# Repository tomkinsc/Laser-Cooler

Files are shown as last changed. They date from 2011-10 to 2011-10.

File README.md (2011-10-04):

(Scroll down for images)

This project includes CAD designs for a custom water cooling box with radiator, pump, and fans. It is intended to cool a 40W hobby laser cutter.

This was created to replace a bucket used for cooling. The open water grew algae, and when the bucket system heated up, only passive radiation could cool it.

This design improves cooling, and is constructed using laser-cut plywood, fittings from the hardware store, and commodity PC water cooling parts. It sports variable fan speed, an on/off switch, and a water reservoir. The setup is powered by a computer power supply.

The tolerances are not as tight as they could be, but it works fine.  The panels are held together with M3x16 socket cap screws. The screws are used similar to how they are in the MakerBot design. The side panels are held by friction, but tape can be added to secure them. A future revision might include screws along those edges as well. The tubing is 3/8 ID black vinyl. It's pretty tight inside the box, so correct tubing length is important.

The box is made from 5.5mm Tri-ply from the local big box home improvement store. The enclosure was designed in DraftSight, and cut using my 40W hobby laser. The enclosure is designed to accommodate the following parts (Newegg part numbers):

* 2x Enzotech HF-G1/4-38 Water Cooling Accessory (#N82E16835708034)
* 1x NZXT Sentry-2 5.25" Touch Screen fan controller (#N82E16811992005)
* 1x Swiftech MCP355 12 VDC Pump (#N82E16835108097)
* 1x Rosewill SL-300TFX 300W TFX12V Power Supply - OEM (#N82E16817182207)
* 2x Scythe SY1225SL12SH 120mm "Slipstream" Case Fan (#N82E16835185060)
* 1x Swiftech MCR220-QP Liquid Cooler Radiator (#N82E16835108086)
* 1x Regular GE wall switch
* 1x Reservoir assembly fashioned from PVC pipe and brass fittings.

The main power switch closes a circuit between lines 14 and 15 on the ATX power supply connector. This turns the supply on. The coolant loop travels as follows: reservoir-->pump->laser tube->radiator->reservoir. It is important to prime the pump so that it does not self destruct. A drain valve on the pump out line works well for this, if the valve is located below the reservoir.

The files are released under a Creative Commons Attribution-NonCommercial-ShareAlike 3.0 Unported License.

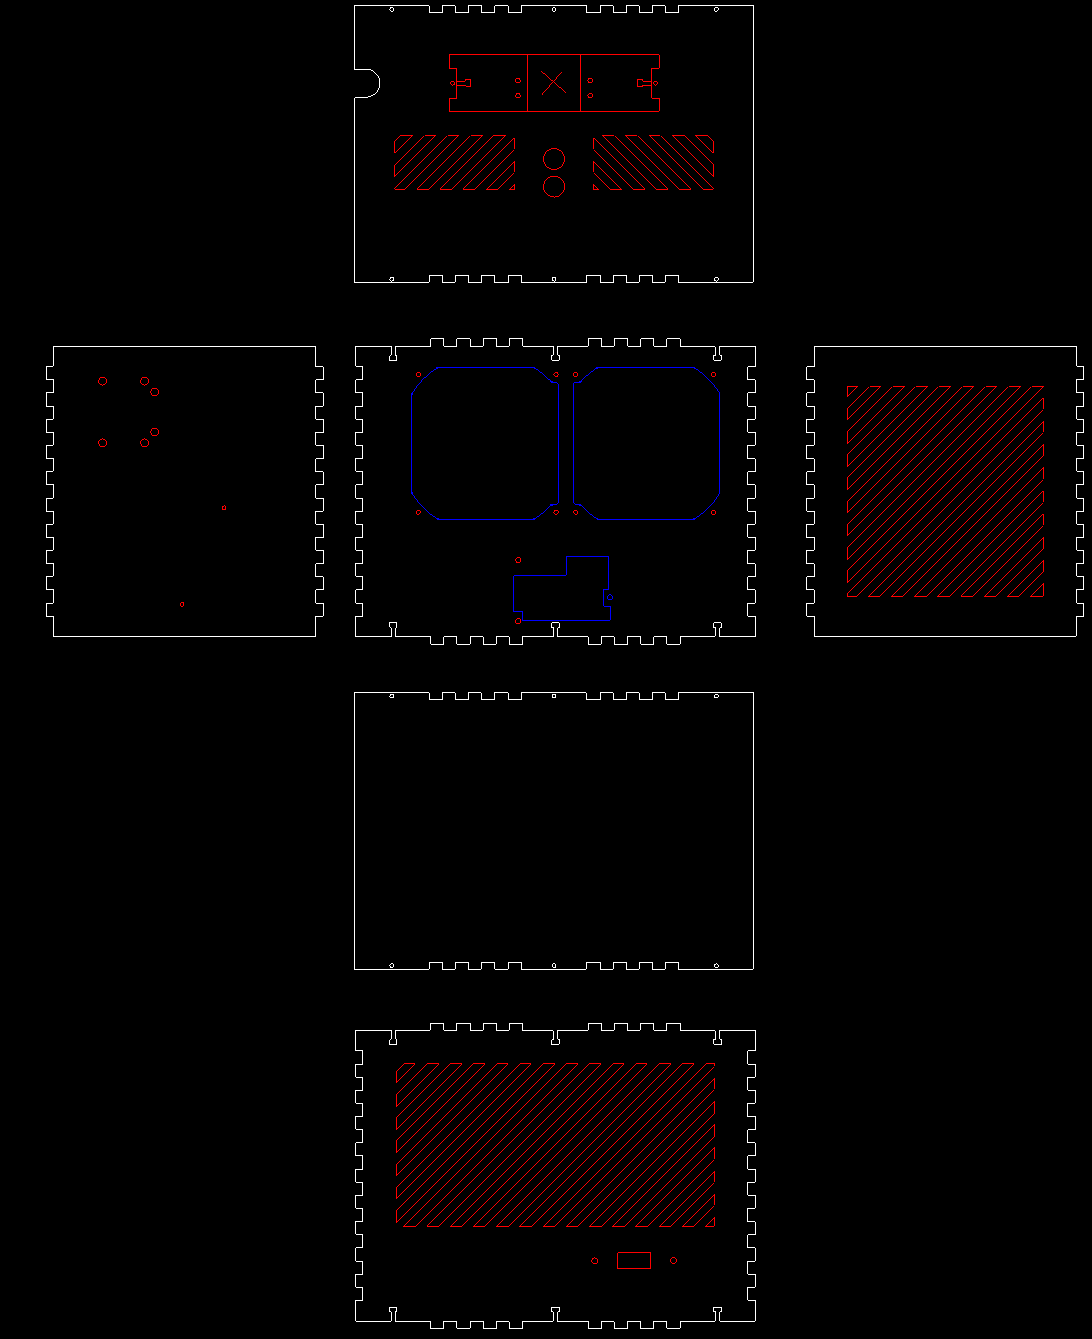
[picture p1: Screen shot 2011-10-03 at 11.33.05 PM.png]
 
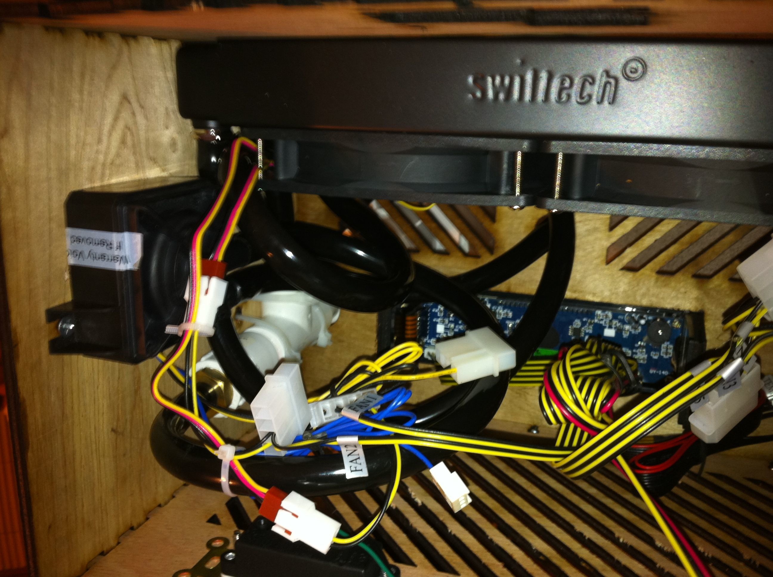
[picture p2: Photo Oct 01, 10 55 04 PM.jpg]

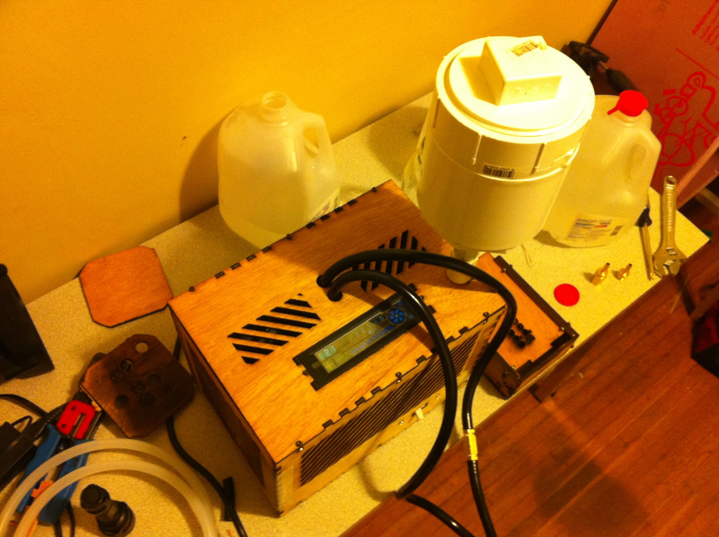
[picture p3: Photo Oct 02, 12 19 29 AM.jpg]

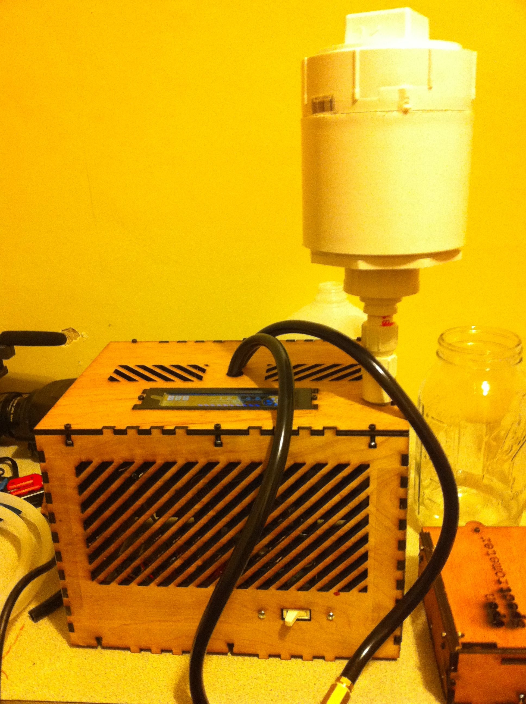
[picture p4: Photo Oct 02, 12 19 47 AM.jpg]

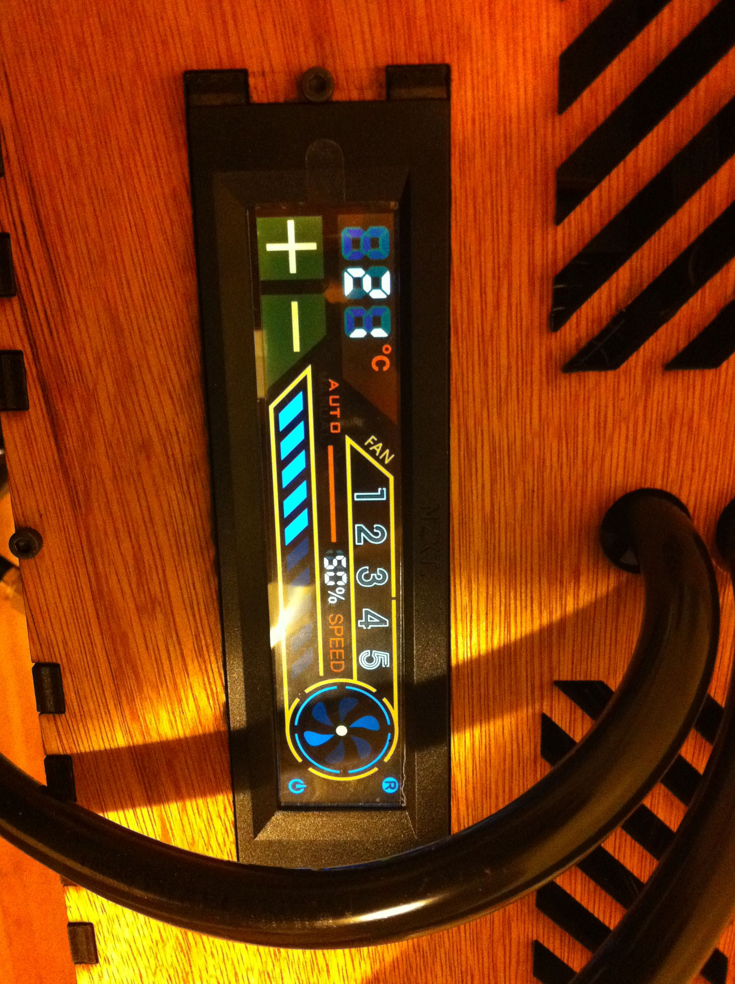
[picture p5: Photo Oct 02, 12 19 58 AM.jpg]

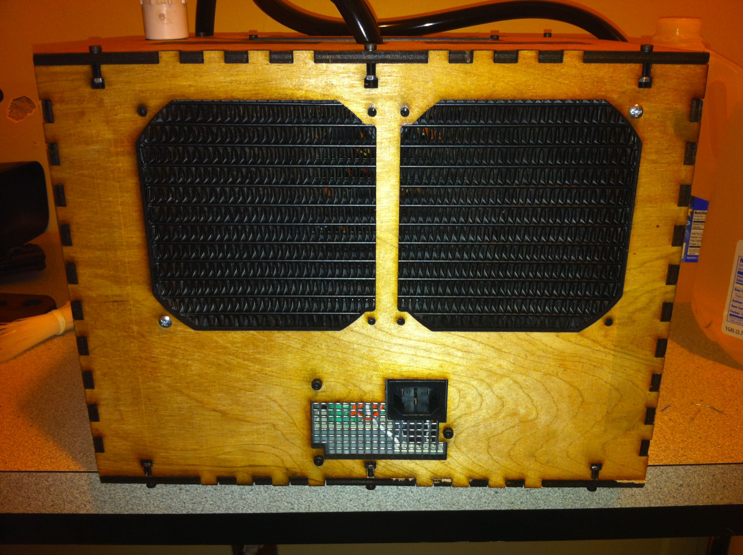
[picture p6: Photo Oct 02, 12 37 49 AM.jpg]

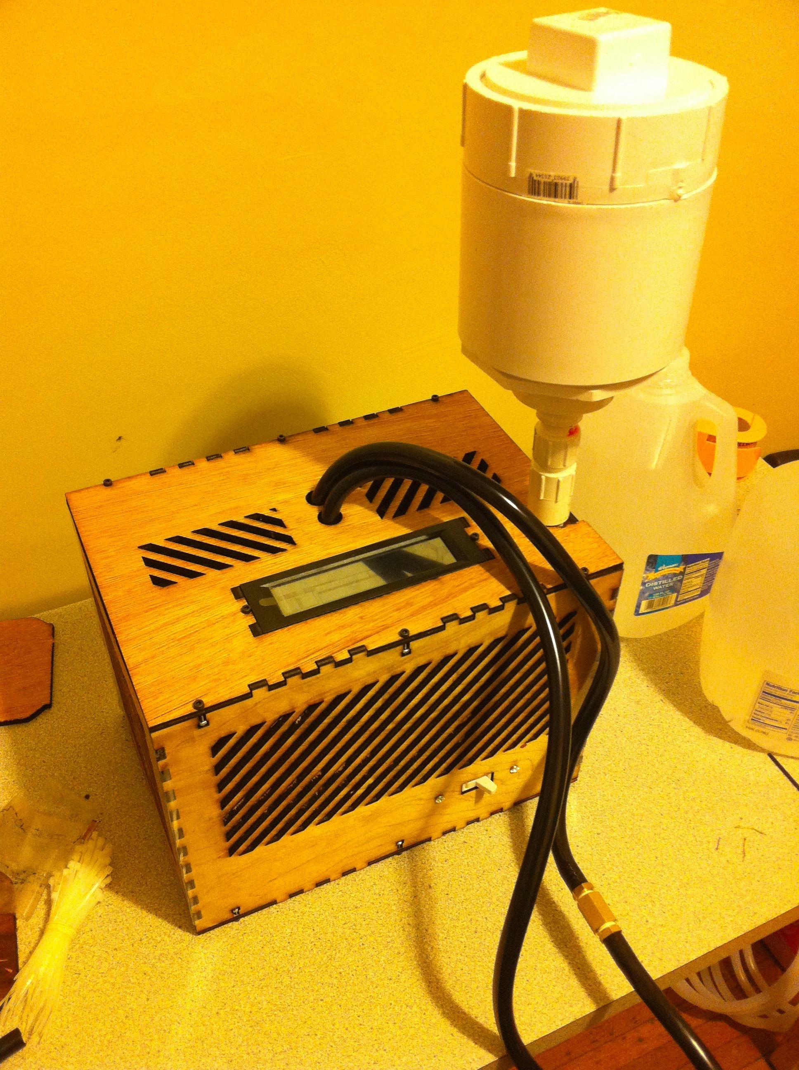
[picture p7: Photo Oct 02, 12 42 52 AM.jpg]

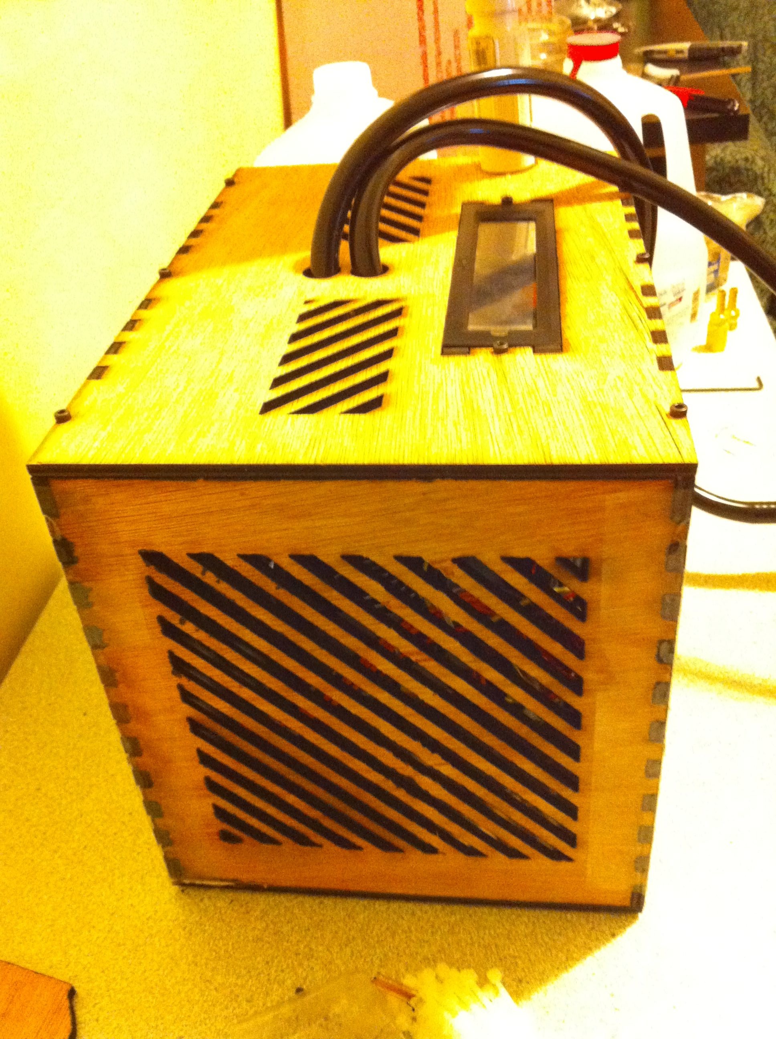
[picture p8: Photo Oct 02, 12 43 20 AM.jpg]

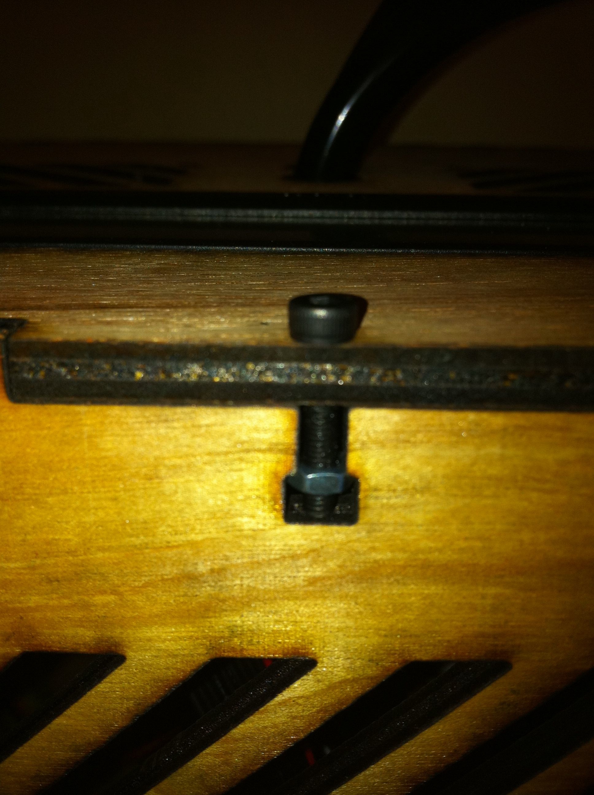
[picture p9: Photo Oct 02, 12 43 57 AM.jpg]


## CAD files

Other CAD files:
laser_cooler_box_vented.dwg

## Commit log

2011-10-04 initial commit of CAD design, README, and LICENSE
    [laser_cooler_box_vented.dwg]
2011-10-04 added project photos for assembly reference
